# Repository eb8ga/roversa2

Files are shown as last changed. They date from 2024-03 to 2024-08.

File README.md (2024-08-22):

# Roversa

Latest repo for the Roversa robot platform

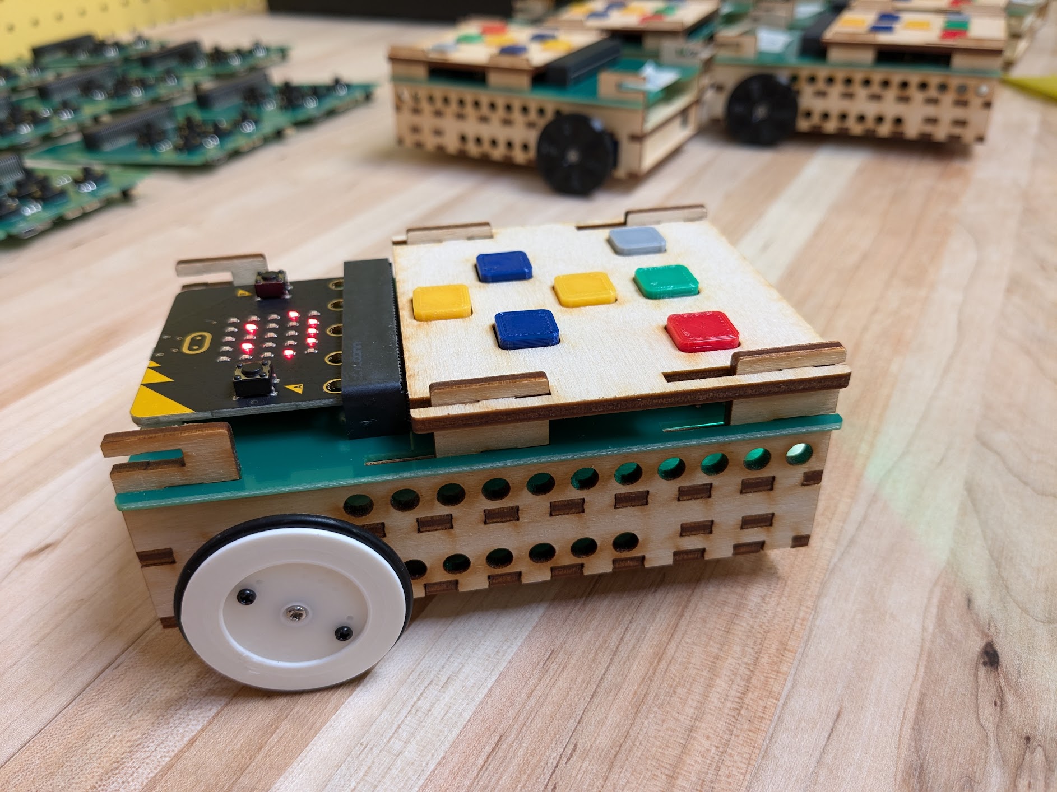
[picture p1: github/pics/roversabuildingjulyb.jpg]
Roversa v 2.1.2


You can use the hex files as a stand-alone version in the releases or the `programming` folder or you can create your own robot using the [MakeCode Extension: Roversa](https://makecode.microbit.org/pkg/eb8ga/pxt-roversa-2)

| **Item** | **Component** | **Quantity** |
|---|---|---|
| Servo Horn Screws | M1.7x4mm, Pan Head, Flat Point | 4 |
| Continuous Servo Motors | FS90R | 2 |
| LiPo Battery | 400 mAh | 1 |
| Ball Bearing | 12mm, G100 Stainless Steel | 1 |
| Tires for Wheels | Nitrile Rubber O-Rings, 35mm OD 30mm ID 2.5mm Width | 2 |
| micro:bit | v2 | 1 |

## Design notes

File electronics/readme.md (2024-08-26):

### This folder contains all of the files for the electronics

**Board Overview:**
Front             |  Rear
:-------------------------:|:-------------------------:
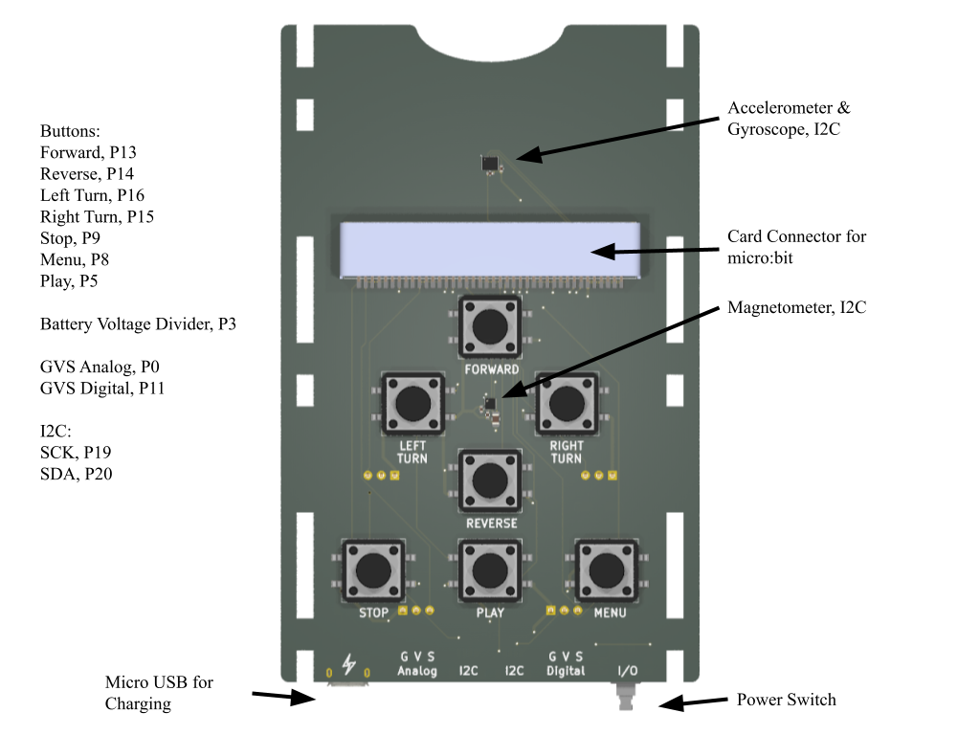
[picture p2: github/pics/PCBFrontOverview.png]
FrontPCB
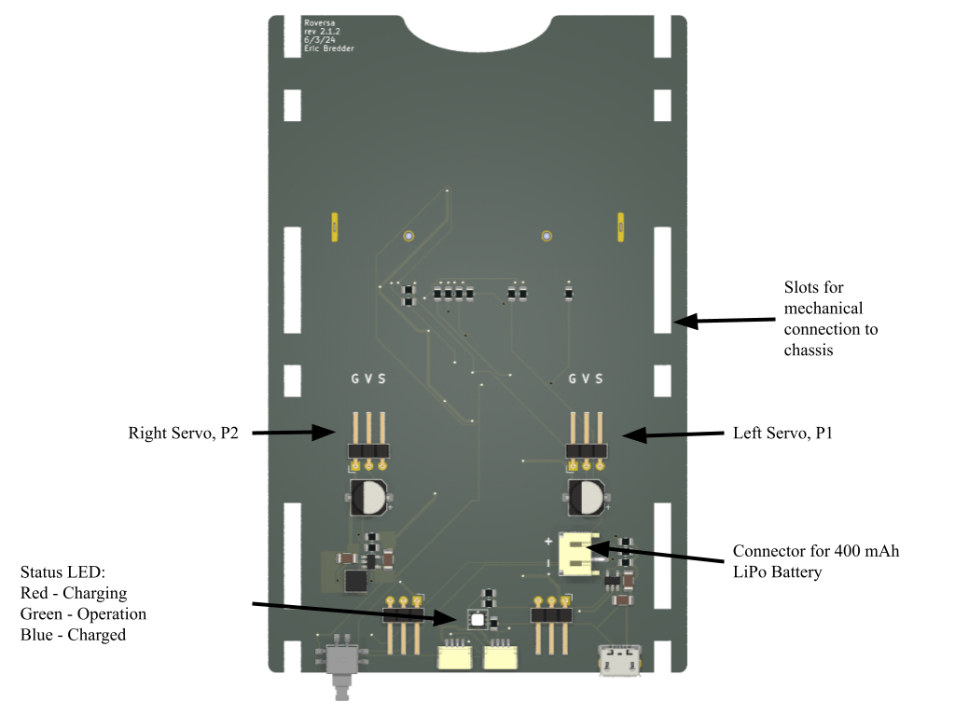
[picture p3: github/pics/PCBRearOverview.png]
RearPCB
 | 

Pinout Diagram:

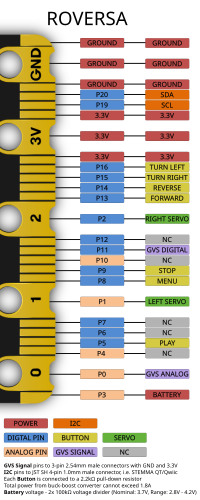
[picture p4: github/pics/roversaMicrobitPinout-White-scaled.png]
Pinout


[Full-size image](https://raw.githubusercontent.com/eb8ga/roversa2/main/github/pics/roversaMicrobitPinout-White.png)

Components:

| **Comment** | **Designator** | **Footprint** |
|---|---|---|
| LSM6DS3TR-C | U4 | LGA-12(2x2) |
| LIS3MDLTR | U3 | LGA-14(2.5x3) |
| MCP73831T-2ACI/OT  | U2 | SOT-23-5 |
| TLV62569DBVR | U1 | SOT-23-5 |
| SW_Push | SW8,SW7,SW6,SW5,SW4,SW3,SW2 | SMD,12x12mm |
| DPDT_LATCH | SW1 | SMD |
| 420 Ω | R17 | 0805 |
| 2.2 kΩ | R16,R15,R14,R13,R12,R11,R10 | 0805 |
| 4.7 kΩ | R9,R8 | 0805 |
| 5 kΩ | R7 | 0805 |
| 100 kΩ | R6,R5,R2 | 0805 |
| 50 Ω | R4 | 0805 |
| 200 Ω | R3 | 0805 |
| 442 kΩ | R1 | 0805 |
| 2.2 μH | L1 | SMD,4x4x3mm |
| GVS | J8,J5 | 3P,P=2.54mm |
| SERVO | J7,J6 | 3P,P=2.54mm |
| JST SH 1.0 | J4,J3 | SMD,P=1mm |
| JST PH 2.0 | J2 | SMD,P=2mm |
| USB_B_Micro | J1 | SMD |
| 40P Edge Connecter | EC1 | MIC127-140-001 |
| LED_RGB | D1 | SMD,2.7x2.8mm |
| 100 μF | C11,C10 | SMD,D6.3xL5.4mm |
| .1 μF | C9,C8,C7,C5 | 0402 |
| 1 μF | C6 | 0805 |
| 10 μF | C4,C3 | 1206 |
| 22 μF | C2 | 1206 |
| 4.7 μF | C1 | 1206 |

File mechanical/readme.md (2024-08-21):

### This folder contains all of the parts for the mechanical components

The laser cut folder has all the pieces in DXF and STEP format. It also has files that accomodate 3mm and 1/8" stock (we found our tolerances at 3.2mm fit the 1/8" plywood well). 

The 3D Print folder has all the remaining parts, wheels, battery holder, bearing support, and the butttons for the keypad.

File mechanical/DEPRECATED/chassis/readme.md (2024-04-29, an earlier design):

### This folder contains all of the parts to create the chassis of Roversa for laser cutting

DXF 2D files for laser cutting and STEP 3D files for any CAD program etc

All parts in this folder must be cut out of **3mm stock material!** The plywood used in the main picture was sold as 3mm or 1/8" but measured an average of 2.88mm thick and was a tight fit. The accuracy of your laser and kerf will also be a factor when adjusting for tolerances. You will have a lot of trouble if your stock measures larger than 3.05mm.

`bottom` is the bottom piece of the chassis

`shelf` is the mid plane of the chassis

`wheelBase` is the part that holds the ball bearing assembly to the chassis

`side_x2` are the sides of the robot, they are identical, they can be mirrored so that the finish on the robot is similar, and you will need 2 of these - you can drill the holes that mount the servo motors out with a 1.60mm or 1/16" drill bit for the M2 screws

`servoSupport_x2` are the pieces that sit behind each servo motor to hold them square and securely in place, these are identical and you will need 2 of these

If you wish to laser cut multiple robots, we have provided a template to get you started. 

`roversaLaserCut2.1-logo-x4.svg` and `roversaLaserCut2.1-logo-x4.ai` will give you flatpack versions of the robot with 4 robots. These 4 will fit on on 300x600mm sheet of material.

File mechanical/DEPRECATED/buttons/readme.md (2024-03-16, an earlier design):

### This folder contains various buttons that can be printed for Roversa

Straight Arrow Button:

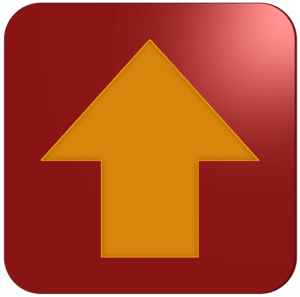
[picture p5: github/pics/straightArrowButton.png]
Straight Arrow Button


Turn Arrow Button:

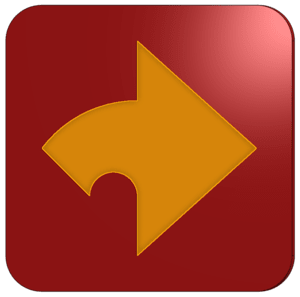
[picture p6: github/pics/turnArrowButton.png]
Turn Arrow Button


Play Button:

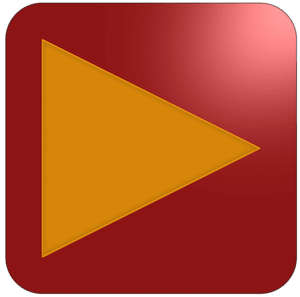
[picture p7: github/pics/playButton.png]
Play Button


Menu Button:

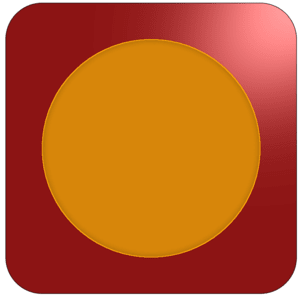
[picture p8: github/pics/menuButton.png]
Menu Button


Stop Button:

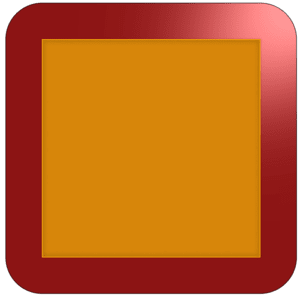
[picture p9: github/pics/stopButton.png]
Stop Button


Pause Button:

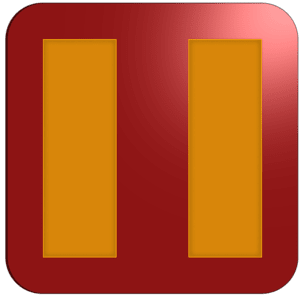
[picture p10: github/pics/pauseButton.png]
Pause Button


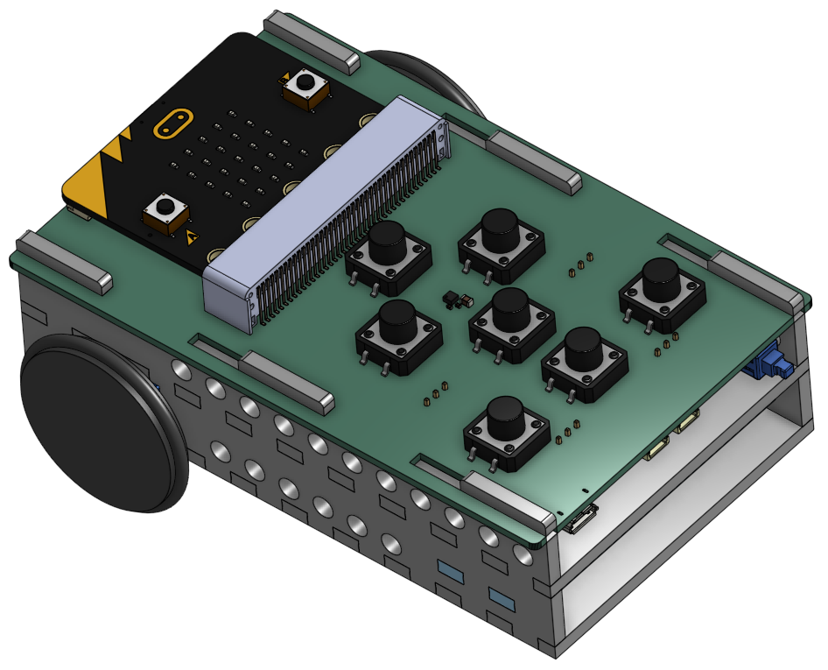
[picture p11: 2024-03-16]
github/pics/CADView.png

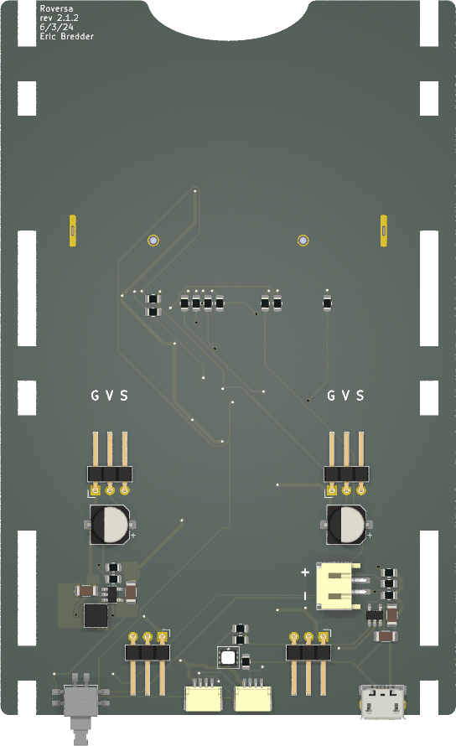
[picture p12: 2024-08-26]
github/pics/roversaPCBv2.1.2Rear.png

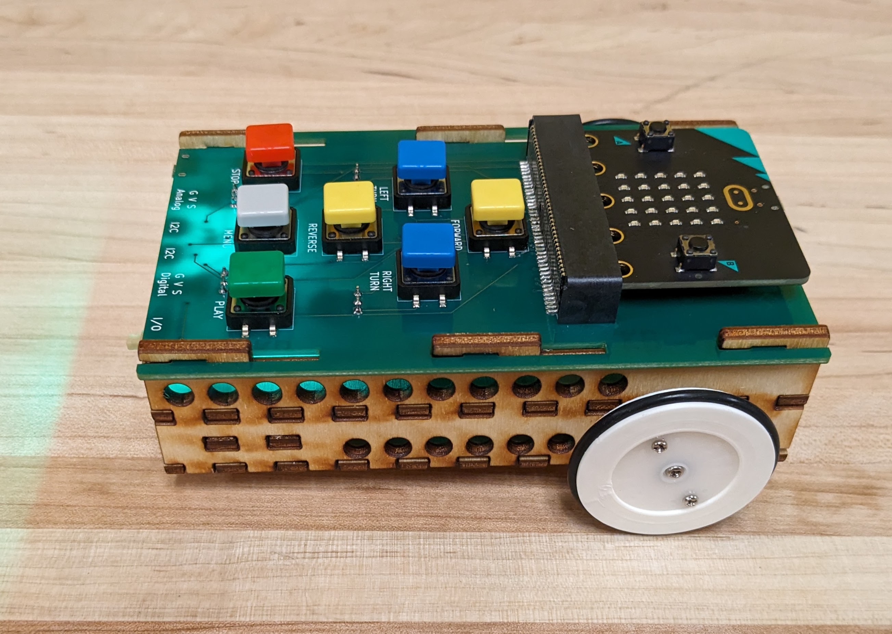
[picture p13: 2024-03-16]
github/pics/sideView.jpg

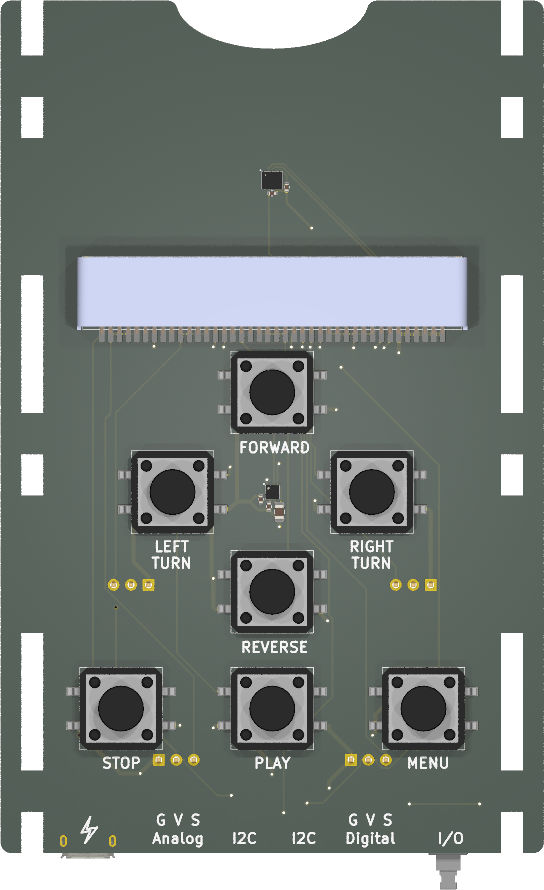
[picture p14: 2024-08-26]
github/pics/roversaPCBv2.1.2Front.png

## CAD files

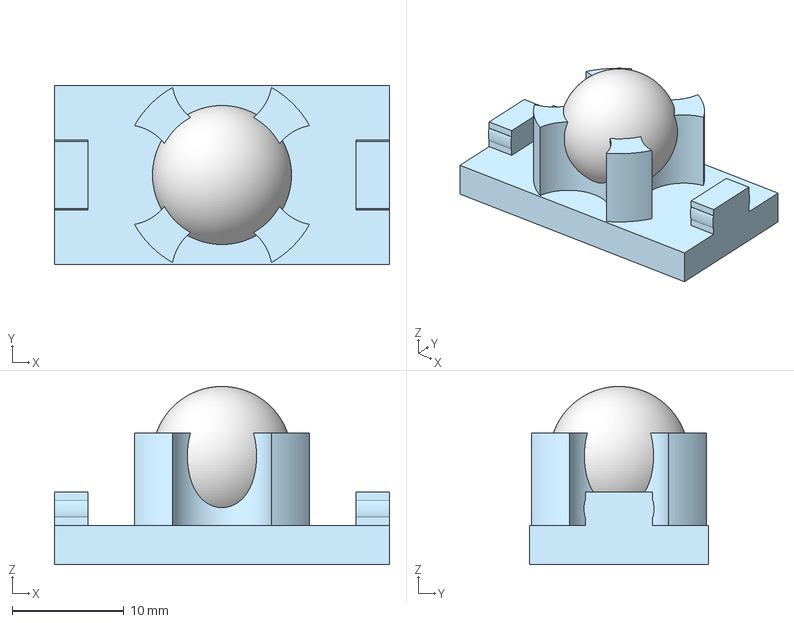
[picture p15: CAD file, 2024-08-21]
mechanical/3D Print/bearingHolder.3mf
30.0 x 16.0 x 15.9 mm
Rear Wheel Bracket
Ball Bearing

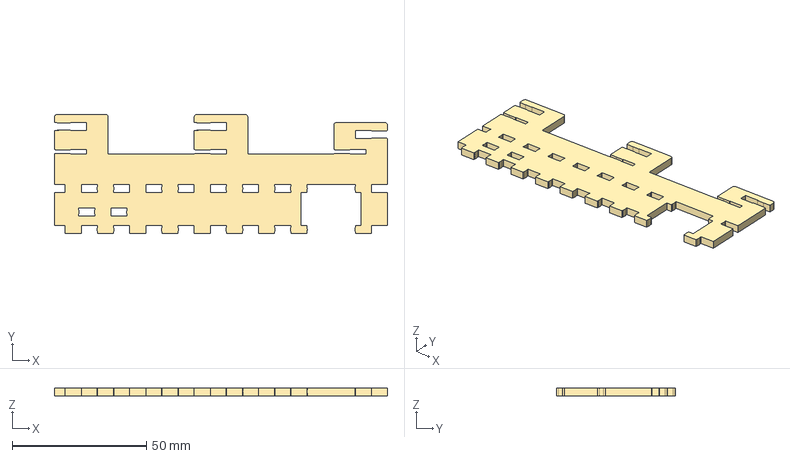
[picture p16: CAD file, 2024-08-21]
mechanical/Laser Cut/3 mm/side_x2_3.0.step
124.0 x 44.4 x 3.00 mm

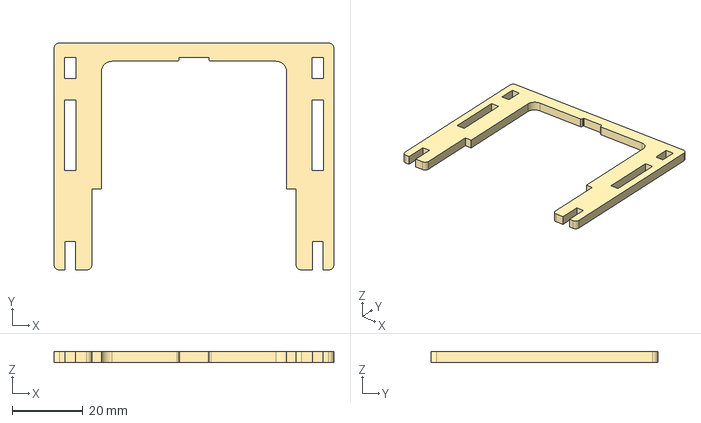
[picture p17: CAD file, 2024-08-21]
mechanical/Laser Cut/3.2 mm/microbitCover_3.2.step
79.0 x 64.0 x 3.20 mm

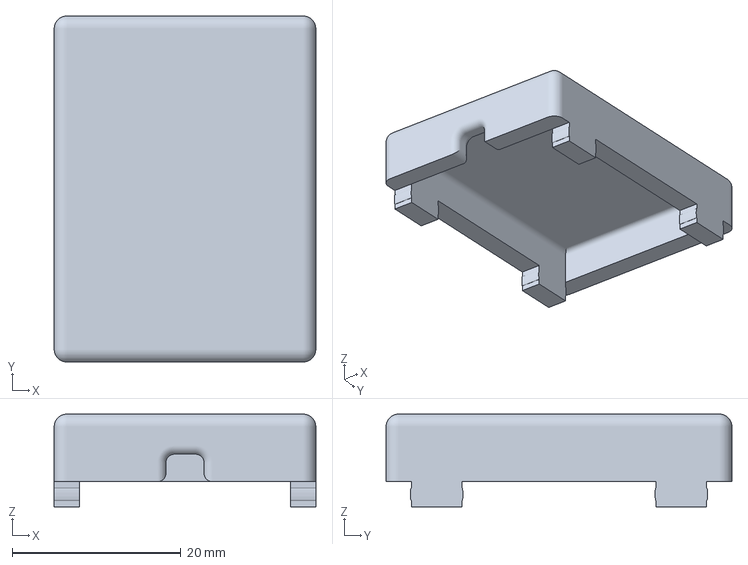
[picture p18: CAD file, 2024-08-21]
mechanical/3D Print/batteryHolder-30x32x5.3mf
31.0 x 41.0 x 11.0 mm

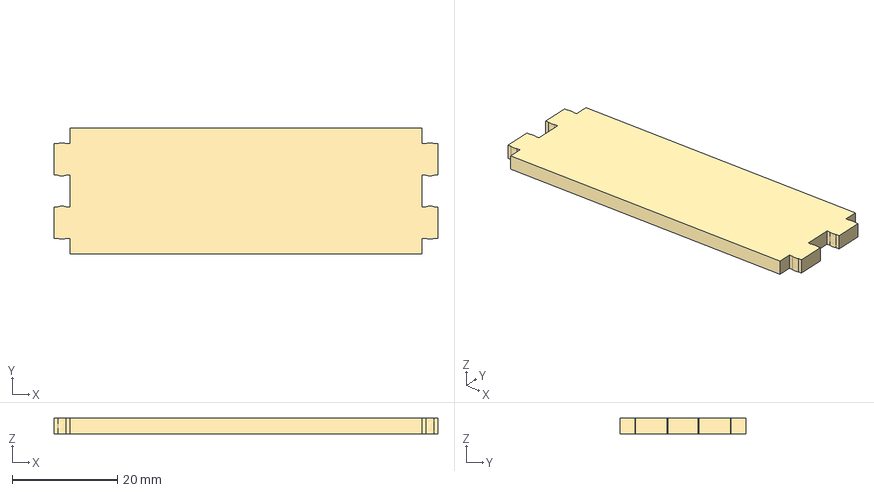
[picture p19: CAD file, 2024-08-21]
mechanical/Laser Cut/3 mm/wheelBase_3.0.step
73.0 x 24.0 x 3.00 mm

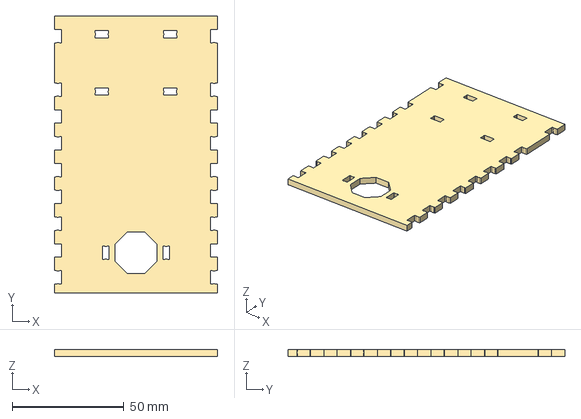
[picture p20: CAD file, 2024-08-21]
mechanical/Laser Cut/3.2 mm/bottom_3.2.step
73.0 x 124.0 x 3.20 mm

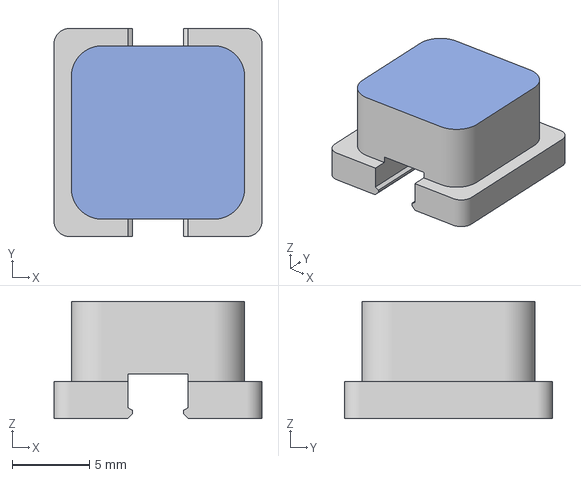
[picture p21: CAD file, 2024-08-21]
mechanical/3D Print/slideButton.3mf
13.5 x 13.5 x 7.60 mm

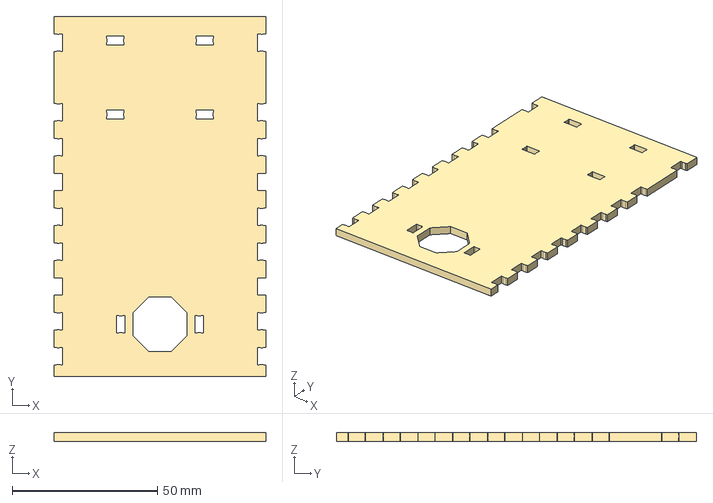
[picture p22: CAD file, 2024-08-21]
mechanical/Laser Cut/3 mm/bottom_3.0.step
73.0 x 124.0 x 3.00 mm

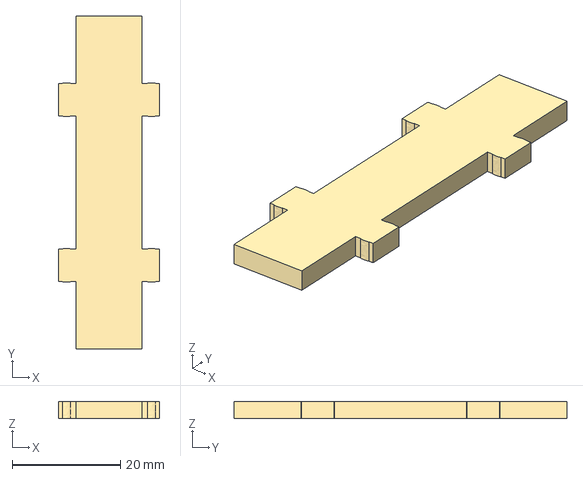
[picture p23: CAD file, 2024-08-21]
mechanical/Laser Cut/3.2 mm/servoSupport_noSlots_3.2.step
18.7 x 61.6 x 3.20 mm

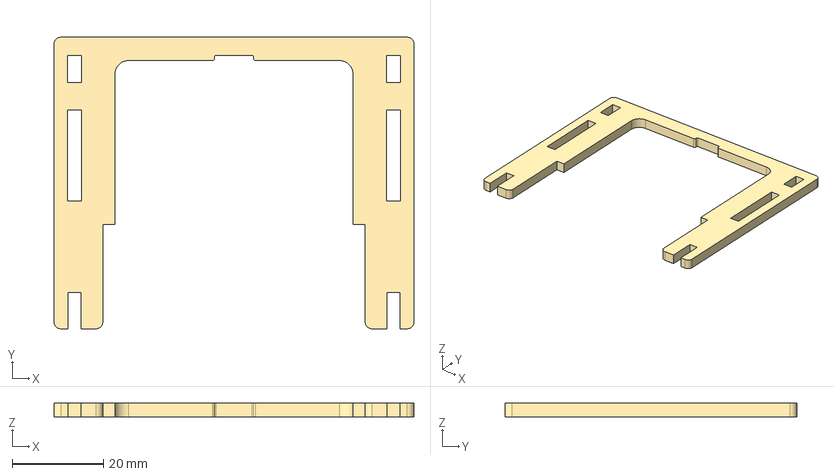
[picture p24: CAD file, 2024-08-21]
mechanical/Laser Cut/3 mm/microbitCover_3.0.step
79.0 x 64.0 x 3.00 mm

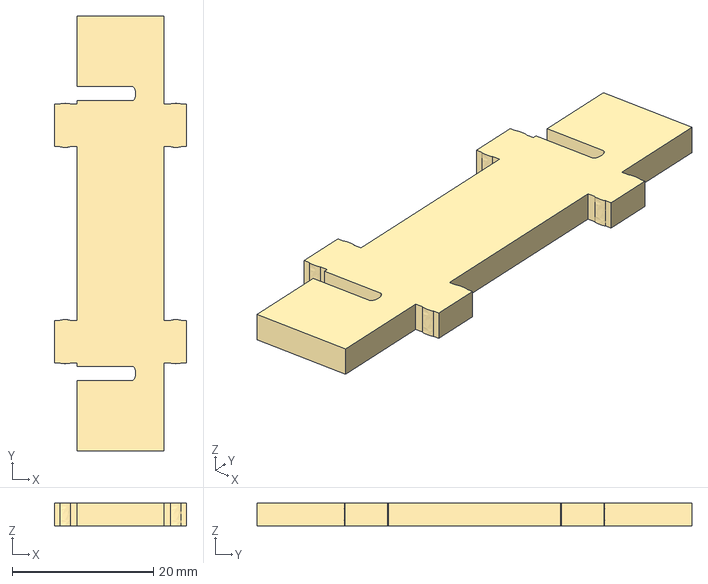
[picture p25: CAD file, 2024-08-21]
mechanical/Laser Cut/3.2 mm/servoSupport_withSlots_3.2.step
18.7 x 61.6 x 3.20 mm

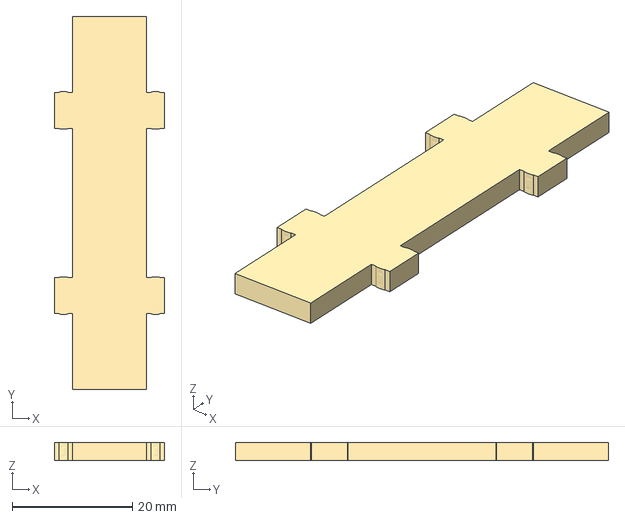
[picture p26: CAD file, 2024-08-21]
mechanical/Laser Cut/3 mm/servoSupport_noSlots_3.0.step
18.3 x 62.0 x 3.00 mm

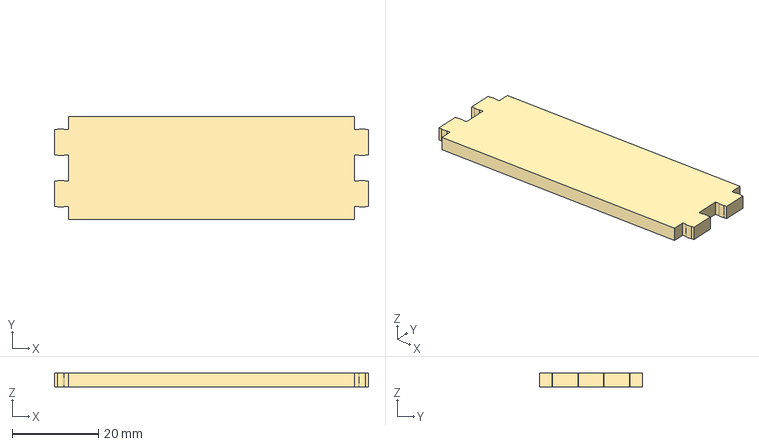
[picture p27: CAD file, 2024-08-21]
mechanical/Laser Cut/3.2 mm/wheelBase_3.2.step
73.0 x 24.0 x 3.20 mm

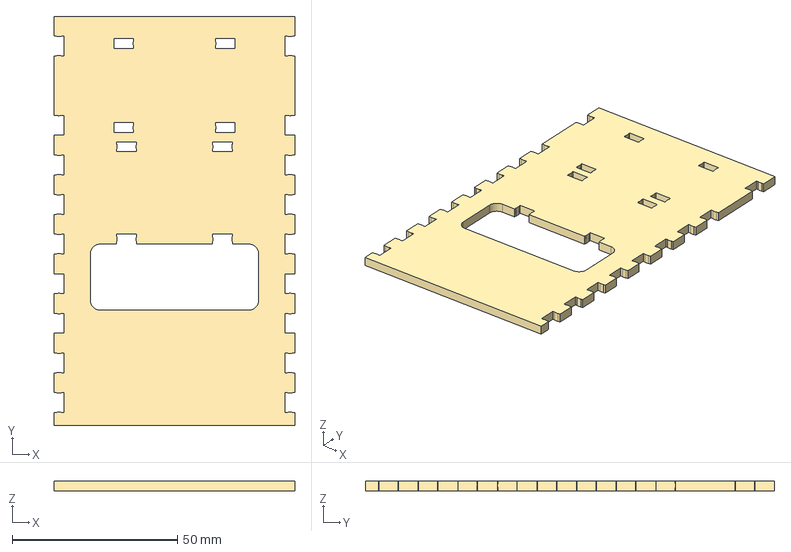
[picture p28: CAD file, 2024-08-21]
mechanical/Laser Cut/3 mm/shelf_3.0.step
73.0 x 124.0 x 3.00 mm

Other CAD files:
mechanical/3D Print/batteryHolder-SF13851.3mf
mechanical/Laser Cut/3.2 mm/keyboardCover_3.2.step
mechanical/Laser Cut/3 mm/servoSupport_withSlots_3.0.step
mechanical/Laser Cut/3.2 mm/side_x2_3.2.step
mechanical/DEPRECATED/batteryHolder-SF13851.3mf
mechanical/DEPRECATED/bearingHolder_x1.amf
mechanical/DEPRECATED/buttons/12mmButtonMenu.3mf
mechanical/DEPRECATED/buttons/12mmButtonPause.3mf
mechanical/DEPRECATED/buttons/12mmButtonPlay.3mf
mechanical/DEPRECATED/buttons/12mmButtonStop.3mf
mechanical/DEPRECATED/buttons/12mmButtonStraightArrow.3mf
mechanical/DEPRECATED/buttons/12mmButtonTurn.3mf
mechanical/DEPRECATED/chassis/bottom.dxf
mechanical/DEPRECATED/chassis/bottom.step
mechanical/DEPRECATED/chassis/servoSupport_x2.dxf
mechanical/DEPRECATED/chassis/servoSupport_x2.step
mechanical/DEPRECATED/chassis/shelf.dxf
mechanical/DEPRECATED/chassis/shelf.step
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

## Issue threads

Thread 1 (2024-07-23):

Ball Bearing too loose

eb8ga, 2024-07-23:
Please make sure to cahnge tolerance on ball bearing

Closed 2024-07-23.

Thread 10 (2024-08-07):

Feature: FinchBlocks/Bluetooth Implementation

techkim, 2024-08-07:
Recompile firmware to match our bot, create custom blocks to control robot, change DC control to servo, remap button configs, create setups for buttons, live control through app, additional gyroscope features

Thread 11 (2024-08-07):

Feature: Gyroscope

techkim, 2024-08-07:
I2c protocol in firmware, create calibration with start of program, add mounting holes to chassis, create custom shapes outside of 180 and 90 deg movements. [Micropython IMU Library](https://github.com/micropython-IMU/micropython-mpu9x50) - [CircuitPython Library](https://github.com/adafruit/Adafruit_CircuitPython_MPU6050) -[ adafruit MPU6050 Guide](https://learn.adafruit.com/lsm303-accelerometer-slash-compass-breakout/python-circuitpython)

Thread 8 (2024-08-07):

Feature: Servo Easing/Smoothing

techkim, 2024-08-07:
[microPython Library](https://github.com/TTitanUA/micropython_servo_pdm_360/tree/main), or [circuitPython example](https://github.com/todbot/circuitpython-tricks#control-a-servo-with-animation-list), [arduino example](https://github.com/XRobots/ServoSmoothing)

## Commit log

2024-03-16 Update and rename Servo-wheelx2(1).amf to servoWheel_x2.amf
    [servoWheel_x2.amf]
2024-03-16 Update and rename bearingHolderx1(1).amf to bearingHolder_x1.amf
    [bearingHolder_x1.amf]
2024-03-16 Rename Screenshot from 2024-03-16 15-33-30.png to boardOverview.png
2024-08-21 v2.1.2 Updated files
    [12mmButtonMenu.3mf, 12mmButtonPause.3mf, 12mmButtonPlay.3mf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]
2024-08-26 updated PCB pics
